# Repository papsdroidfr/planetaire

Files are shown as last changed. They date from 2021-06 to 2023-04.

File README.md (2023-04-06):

# planétaire

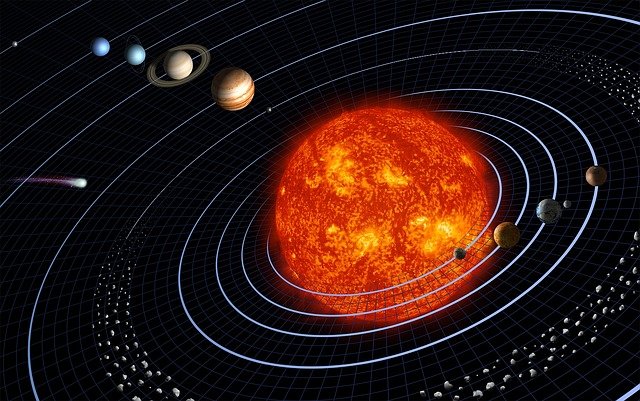
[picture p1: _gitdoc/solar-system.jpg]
système solaire


Ce projet consiste à réaliser un planétaire mécanique à l'échelle d'un bureau, à base d'impression 3D et d'électronique (Raspberry pico)

## cadrage du projet 

Quelques bases concernant [les dimensions](https://papsdroidfr.github.io/tutoriels/planetaire/) du système solaire

Notre planétaire mécanique à l'échelle d'un bureau va:
* représenter les orbites sous forme de cercles
* tricher sur les proportions des orbites et taille de Jupiter et Saturne (et du soleil)
* intégrer les 6 planètes visibles à l’œil nu: Mercure, Vénus, la Terre (et son satellite la lune), Mars, Jupiter et Saturne.

Un peu de théorie avec [les engrenages](https://papsdroidfr.github.io/tutoriels/engrenages/)
* les roues dentées utlisées doivent être limitées en nombre de dents (de 13 à 100)
* les engrenages simples (2 roues dentées) ne permettent pas d'obtenir de gros rapport de réduction R = -d1/d2 (avec 2 roues) ou R = +d1/d3 (avec 3 roues: le nombre de dents de la roue intermédiaire ne compte pas dans le rapport de réduction)
* les engrenages à étage permettent d'aller chercher les gros rapports de réduction selon l'équation:

```python
R = (-1)^y * (Z1 * Z2 *..* Zn) / (D1 * D2 * ... * Dm)
```

* y est le nombre de contacts entre les dents.
* Zi, Dj le nombre de dents d'une roue.
* n le nombre de roue menantes.
* m le nombre de roue menées.

## calcul des réduction d'engrenages 

le programme **engrenage_reduction.py** (dossier /python) calcule la meilleure solution d'engenages sur 2, 3 ou 4 étages pour obtenir un rapport de réduction R donné. Plus de détail dans [cet article](https://papsdroidfr.github.io/dev/CalculEngrenages/).

## Conception des étages d'engrenages par planète

### Mercure
La conception du prototype en 3D est expliquée [ici](https://papsdroidfr.github.io/tutoriels/Planetaire-Mercure/)

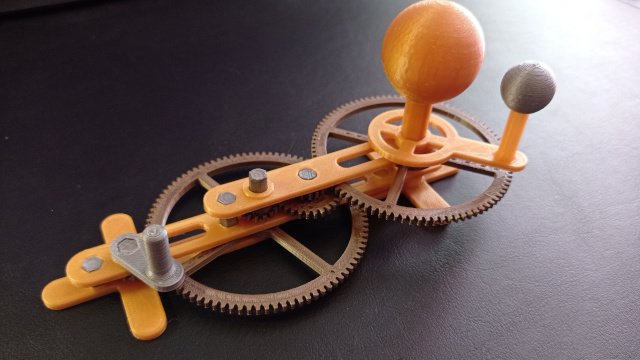
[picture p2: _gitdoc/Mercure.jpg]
Mercure


Ce premier prototype utilise un mécanismue de réduction 1/7 avec une roue de 13 dents contre une roue de 13*7=91 dents afin d'avoir un premier axe qui représente une jounée (celui où l'on retrouve la manivelle) et un second qui représente une semaine. Tous les mécanismes vont partir de l'axe des semaines, les rapports sont donc tous réduits par 7 dès le départ.

Mercure tourne autour du soleil en 87,969 jours ( =12,567 semaines). En utilisant des roues menantes de 14  et 15 dents contre des roues menées de 29 et 91 dents j'obtiens un rapport de réduction de 87,967.

### Vénus
conception du modèle 3D: [ici](https://papsdroidfr.github.io/tutoriels/Planetaire-Venus/)

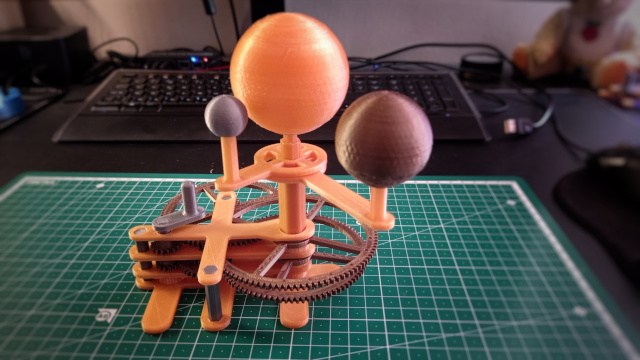
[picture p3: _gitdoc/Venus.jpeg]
Venus


Tous les mécanismes partent désormais de l'axe des semaines avec une réduction de 1/7 dès le départ.
On retrouve donc sur le premier plateau les roues de 14,15, 29 et 91 dents pour obtenir le rapport de réduction 87,967 propre à Mercure 
Le second plateau est quand à lui composé de 2 roues menantes de 16 dents contre des roues menées de 83 et 99 dents afin d'obtenir un rapport de réduction de 224.684 pour Vénus (Vénus tourne autour du soleil en 224,700 jours). On pourrait obtenir une meilleure précision en ajoutant un 2ème étage mais ce gain de précision n'en vaut pas la peine pour cette maquette qui n'a pas vocation à faire des prédictions.
Toutes les planètes sont positionnées sur des plateaux centrés sur des axes creux qui s'emboitent les uns dans les autres.

### Terre
conception du modèle 3D: [ici](https://papsdroidfr.github.io/tutoriels/planetaire-terre/)

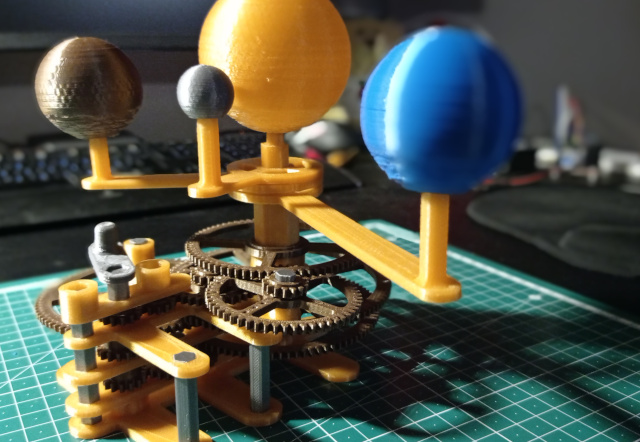
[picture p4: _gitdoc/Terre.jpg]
Terre


Pour rappel, j'utilise un axe commun pour toutes les planètes qui représente 1 semaine (7 jours) par tour complet. Tous les mécanismes héritent de fait de ce premier rapport de réduction de 1/7. Il faut donc viser 7/365,256 comme rapport de réduction. J'utilise mon programme développé en python pour simuler plusieurs solutions de manière à retenir le meilleur compromis entre précision et complexité (nombre d'étages d'engrenages). On arrive à une belle solution avec 2 étages de 3 peties roues menantes de 13, 15 et 15 dents, contre 3 grandes roues menées de 37, 55 et 75 dents. Si vous faites le calcul 7 * ( 37*55*75) / ( 13*15*15) vous verrez que la précision est diaboliquement proche de 365,256. Puisqu'il y a un étage de plus que pour Mercure et Vénus, il faut ajouter une roue inverseuse afin que la Terre tourne dans le même sens que les autres planètes.

### Mars
conception du modèle 3D: [ici](https://papsdroidfr.github.io/tutoriels/planetaire-mars/)

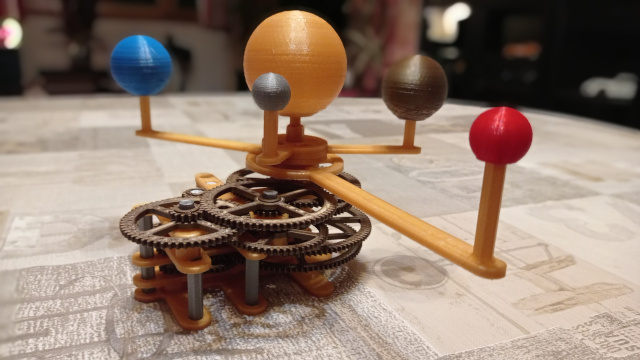
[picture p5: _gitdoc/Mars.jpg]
Mars


Je trouve un très bon compromis avec seulement 2 étages de 3 roues menantes de 14, 15 et 16 dents contre 3 roues menées de 59, 69 et 81 dents. Je rappelle que la première roue menante (celle de 14 dents en l’occurrence) est positionnée sur l'axe de rotation des semaines: il faut donc multiplier le tout par 7 pour avoir le rapport de réduction final: 7*(59*69*81)/(14*15*16) = 686,98125 : pas la peine de se compliquer la vie en rajoutant un 3me étage pour gagner en précision: c'est déjà très précis comme ça quand on vise à obtenir 686.980 ! Enfin une dernière petite astuce pour que Mars tourne dans le même sens que les autres planètes: je pars de l'axe de rotation hebdomadaire déjà inversé du mécanisme de la Terre. L'axe central qui soutient le bras sur lequel Mars est positionnée est quand à lui centré sur l'axe du soleil, et enveloppe les axes respectifs de Mercure, Vénus et celui de la Terre: ils sont tous à l'intérieur.

### Notice de montage 
La notice de montage complète, avec motirisation optionnelle, est décrite [dans cet article](https://papsdroidfr.github.io/tutoriels/planetaire-maquette/)

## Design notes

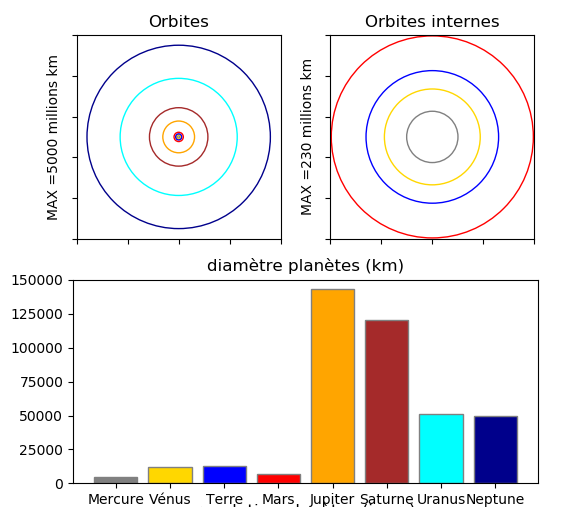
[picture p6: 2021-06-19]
_gitdoc/orbites.png

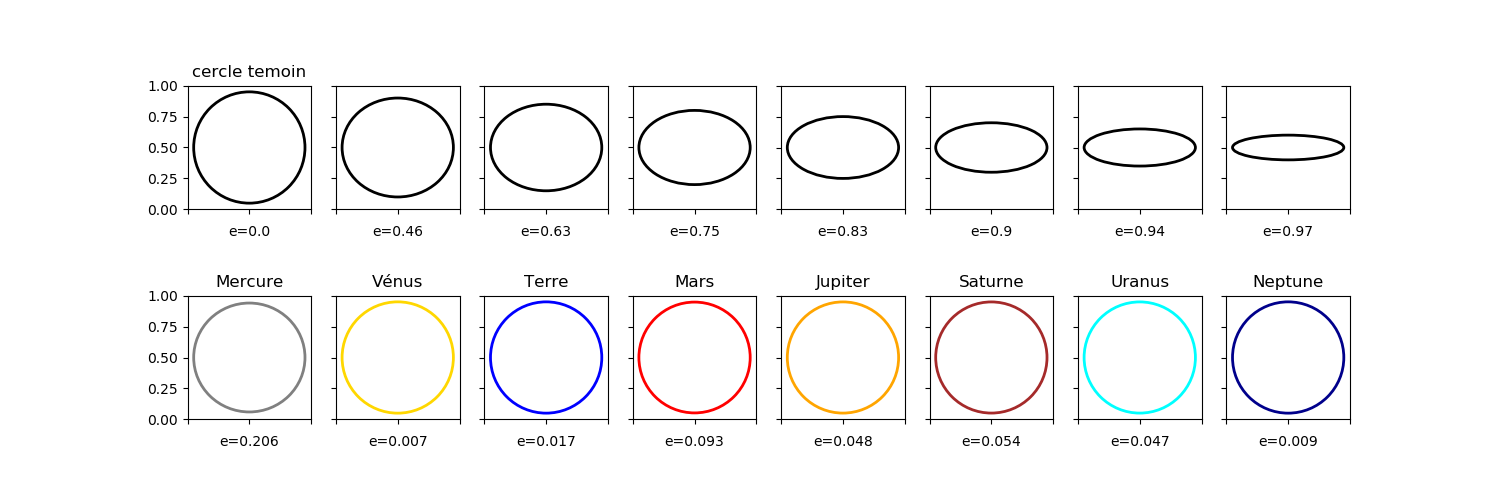
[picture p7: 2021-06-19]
_gitdoc/ellipses.png

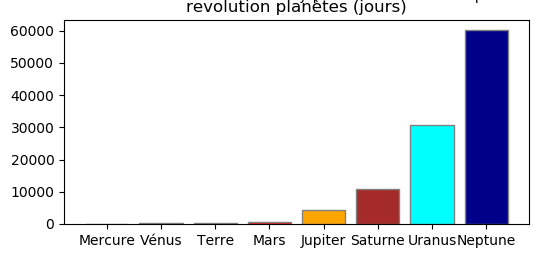
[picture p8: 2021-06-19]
_gitdoc/revolutions.png

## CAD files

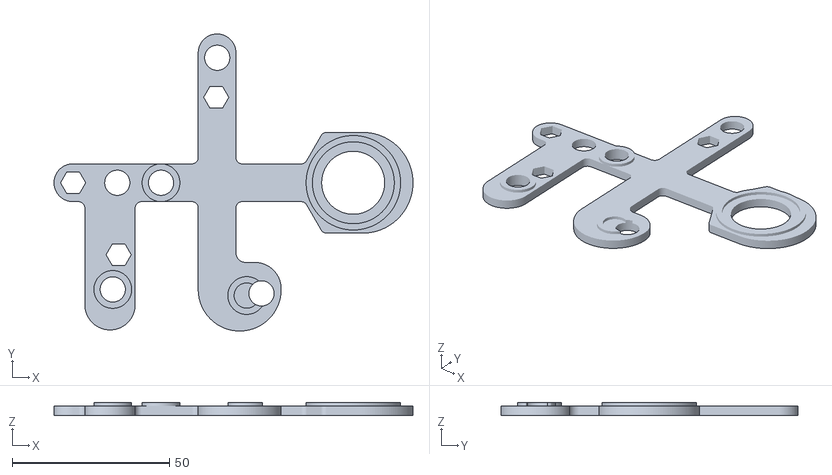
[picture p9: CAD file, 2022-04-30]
STLPlanetaire/Mars/Mars_Support_Bas.stl
114.0 x 94.3 x 4.00

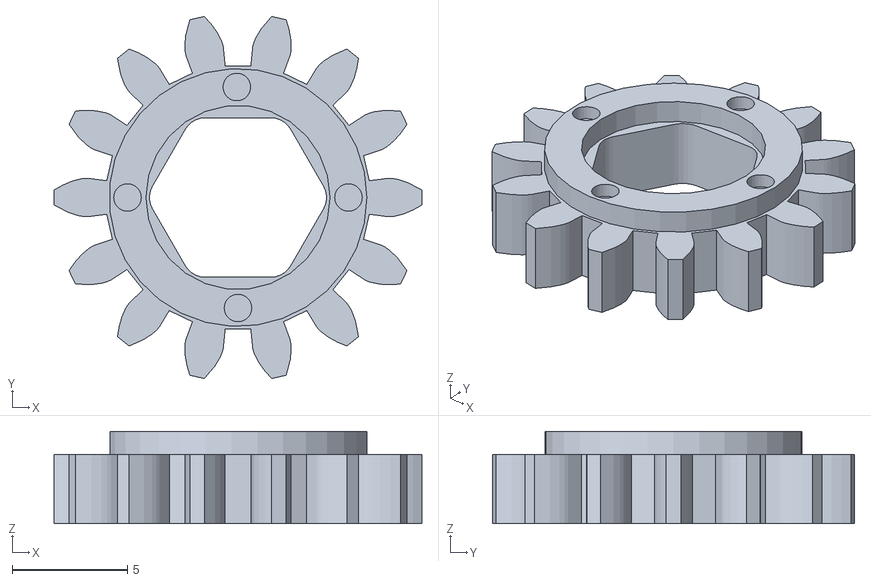
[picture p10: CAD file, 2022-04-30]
STLPlanetaire/Mercure/mercure_gear14.stl
16.0 x 15.7 x 4.00

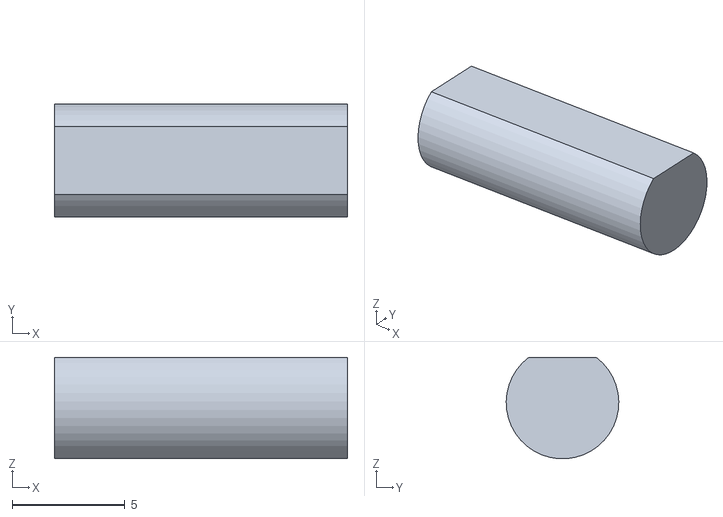
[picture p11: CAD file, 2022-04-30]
STLPlanetaire/MOTOR/moteurSupportAxe.stl
13.0 x 5.00 x 4.49

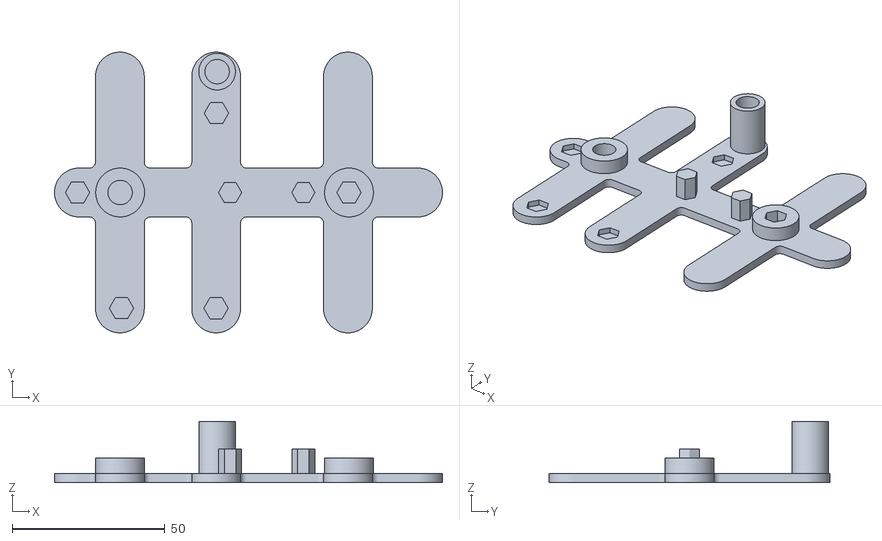
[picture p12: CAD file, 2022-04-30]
STLPlanetaire/Pied/pied_support_bas.stl
127.1 x 92.0 x 20.0

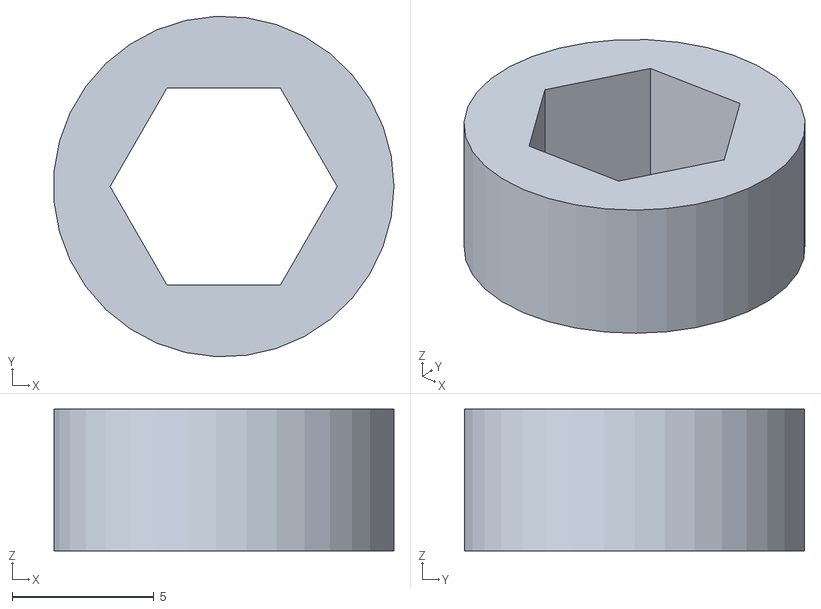
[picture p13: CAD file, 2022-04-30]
STLPlanetaire/Soleil/soleilColeretteAxe.stl
12.0 x 12.0 x 5.00

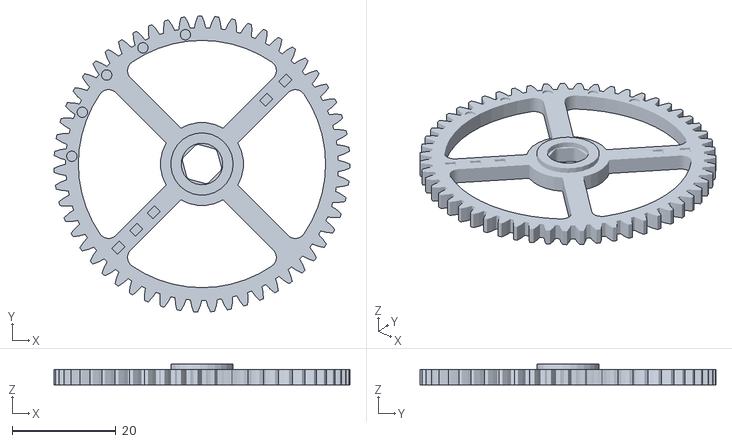
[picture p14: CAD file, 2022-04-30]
STLPlanetaire/Terre/TerreGear55.stl
57.0 x 57.0 x 4.00

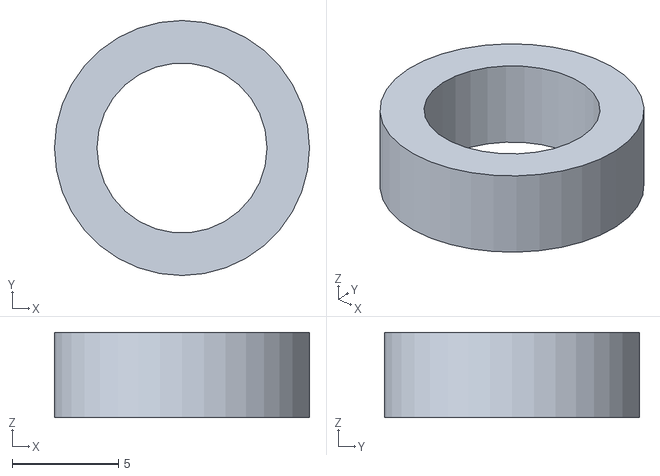
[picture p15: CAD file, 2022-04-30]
STLPlanetaire/Vénus/venus_colerette.stl
12.0 x 12.0 x 4.00

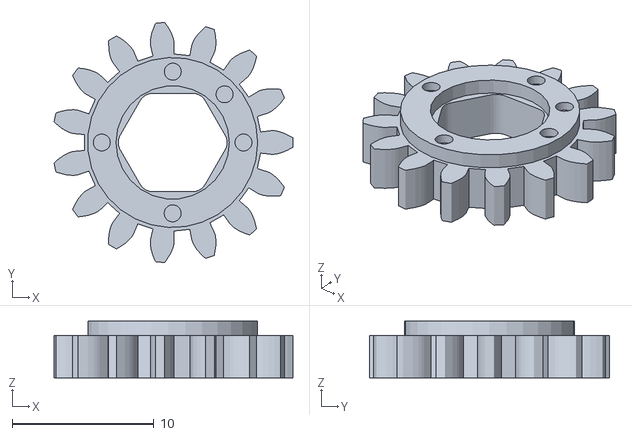
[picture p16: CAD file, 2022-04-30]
STLPlanetaire/Mars/Mars_Gear15.stl
16.9 x 17.0 x 4.00

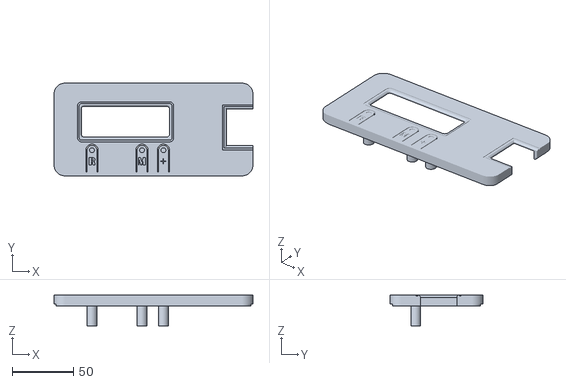
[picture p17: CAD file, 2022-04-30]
STLPlanetaire/MOTOR/BoitierHaut.stl
162.9 x 75.9 x 25.0

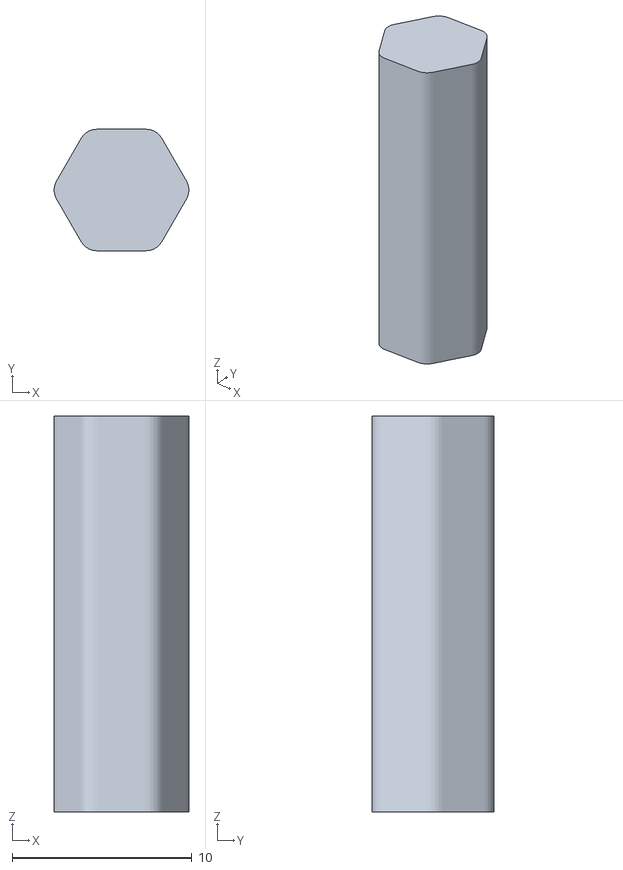
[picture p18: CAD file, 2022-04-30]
STLPlanetaire/Pied/pied_fix3.stl
7.48 x 6.75 x 22.0

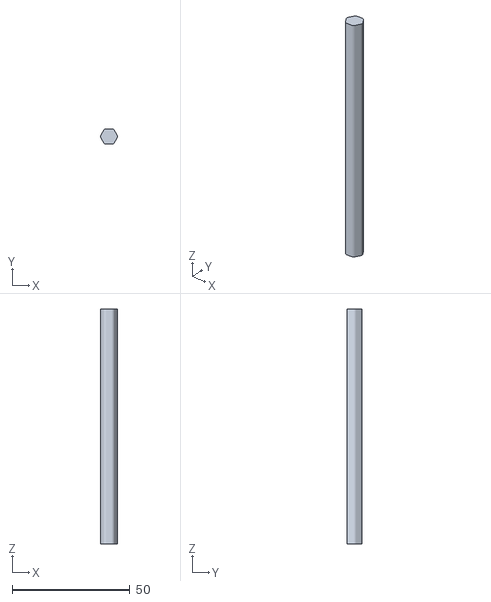
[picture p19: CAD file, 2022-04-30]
STLPlanetaire/Soleil/axeSoleil.stl
7.17 x 6.58 x 100.0

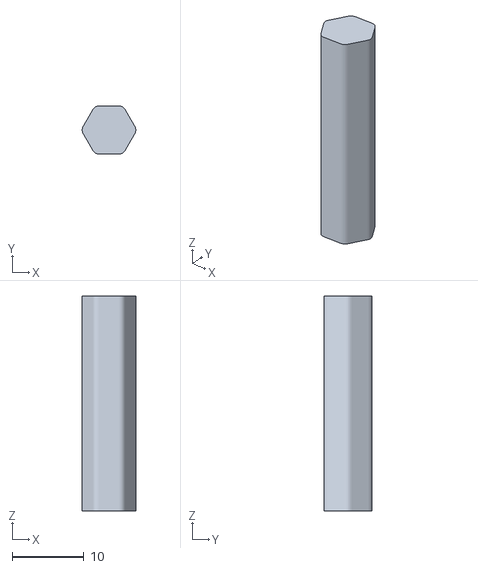
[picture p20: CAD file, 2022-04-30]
STLPlanetaire/Terre/Terre_AxeFix.stl
7.48 x 6.75 x 30.0

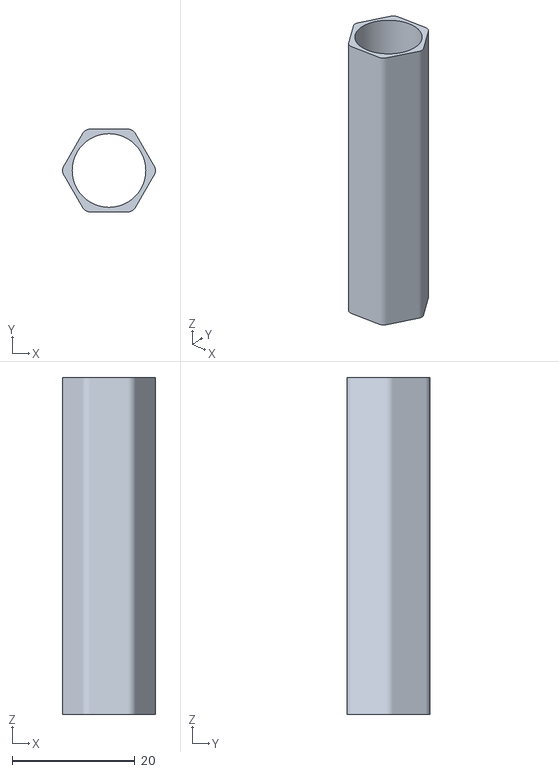
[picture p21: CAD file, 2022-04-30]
STLPlanetaire/Vénus/venus_axe.stl
15.2 x 13.5 x 55.0

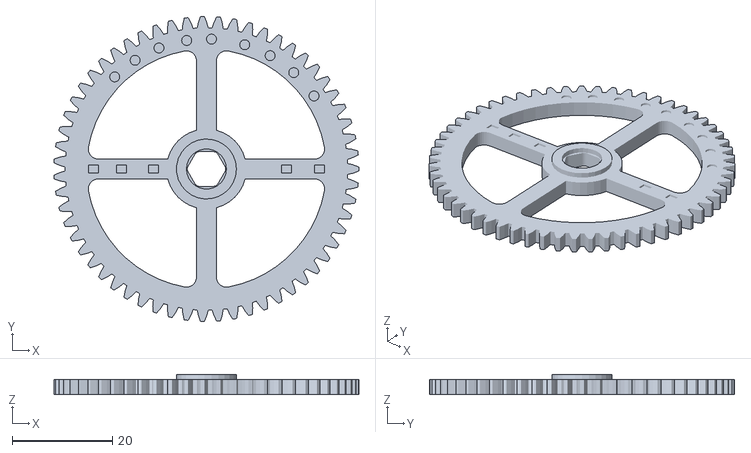
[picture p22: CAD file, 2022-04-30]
STLPlanetaire/Mars/Mars_Gear59.stl
61.0 x 61.0 x 4.00

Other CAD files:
STLPlanetaire/Mercure/mercure_colerette.stl
STLPlanetaire/Mercure/mercureColeretteAxe.stl
STLPlanetaire/MOTOR/moteurGear14.stl
STLPlanetaire/Pied/pied_fix1.stl
STLPlanetaire/MOTOR/BoitierBas.stl
STLPlanetaire/MOTOR/moteurGear16.stl
STLPlanetaire/MOTOR/moteurSupportBas.stl
STLPlanetaire/Mars/MarsColerette4mm.stl
STLPlanetaire/Mars/Mars_Axe_Central.stl
STLPlanetaire/Mars/Mars_Axe_Gear59.stl
STLPlanetaire/Mars/Mars_Axe_Gear69.stl
STLPlanetaire/Mars/Mars_Axe_fix(x2).stl
STLPlanetaire/Mars/Mars_Gear14.stl
STLPlanetaire/Mars/Mars_Gear16.stl
STLPlanetaire/Mars/Mars_Gear69.stl
STLPlanetaire/Mars/Mars_Gear81.stl
STLPlanetaire/Mars/Mars_Panète.stl
STLPlanetaire/Mars/Mars_Plateau.stl
STLPlanetaire/Mars/Mars_Support_Haut.stl
STLPlanetaire/Mercure/Mercure_support_bas.stl
STLPlanetaire/Mercure/mercure.stl
STLPlanetaire/Mercure/mercure_axe_central.stl
STLPlanetaire/Mercure/mercure_axe_gear.stl
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

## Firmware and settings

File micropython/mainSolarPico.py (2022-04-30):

#RUNS ON PICO
from bipolarStepper import BipolarStepper
from machine import Pin, I2C, Timer
from machine_i2c_lcd import I2cLcd
import sys, time, _thread


class MyLCD:
    ''' LCD1602 screen '''
    def __init__(self):
        
        #i2c detection
        i2c = I2C(0, sda=Pin(0), scl=Pin(1), freq=400000)
        l=i2c.scan() #liste les adresses I2C trouvées
        try:   
            i2c_adr = hex(l[0])
            print('Init LCD, adresse I2C: ', i2c_adr)
        except:
            print('aucun LCD I2C trouvé, vérifiez vos branchements...')
            sys.exit()
        
        self.lcd = I2cLcd(i2c, int(i2c_adr), 2, 16)
        
        # generator custom character: http://omerk.github.io/lcdchargen/
        charmap = [
            #chr(0): logo papsdroid
            [0b01110,0b11111,0b10101,0b11111,0b11111,0b10001,0b11111,0b01110],
            #chr(1): fusée
            [0b00100,0b01110,0b01010,0b11111,0b11111,0b11111,0b10101,0b10001],
            #chr(2): pi
            [0b00000,0b00000,0b11111,0b01010,0b01010,0b01010,0b10011,0b00000],
            #chr(3): batterie full
            [0b01110,0b11011,0b10001,0b10101,0b10101,0b10101,0b10001,0b11111],
        ]
        for i in range(len(charmap)):
            self.lcd.custom_char(i,charmap[i])
        
        self.id_day=0    # updated with motor rotation
        self.id_mode=0   # updated with mode change
        self.mode=''     # updated with mode change
    
        self.msg_init()
    
    def msg_init(self):
        '''displsay init message'''
        self.lcd.clear()
        self.lcd.move_to(0,0)
        self.lcd.putchar(chr(0)) #logo paspdroid
        self.lcd.putstr(' PapsDroid.fr ')
        self.lcd.putchar(chr(0))
        self.lcd.putchar(chr(2))
        self.lcd.putstr('\n'+' PICOPLANETES ')
        self.lcd.putchar(chr(2))
        time.sleep(1)
       
    def displ_mode(self):
        ''' display mode'''
        self.lcd.move_to(0,0)
        self.lcd.putstr('Mode: ')
        for _i in range(self.id_mode+1):
            self.lcd.putchar(chr(3))
        for _i in range(4-self.id_mode):
            self.lcd.putchar(' ')
        self.lcd.move_to(12,0)
        self.lcd.putstr(self.mode)
        
        
    def displ_jour(self, _tm):
        '''display day number, called in Timer every 200ms'''
        str_day = str(self.id_day)
        self.lcd.move_to(0,1)
        self.lcd.putstr('Jour: ' + str_day)
    
class Application:
    
    def __init__(self):
        ''' initialize lcd, push Button and stepper motor'''
        self.mylcd = MyLCD();
        self.ledStatus = Pin(25, Pin.OUT)     # led témoin du pico
        self.buttonMode = Pin(18, Pin.IN, Pin.PULL_DOWN) #bouton poussoir avec resistance de rappel activée
        self.buttonNext = Pin(19, Pin.IN, Pin.PULL_DOWN) #bouton poussoir avec resistance de rappel activée
        self.id_mode=0
        self.l_modes = ['+01J', '+07J', '+30J', '+inf']
        self.bouncetime = 0.05 #stabilization period with push buttons
        #callback function called with push buttons
        self.buttonMode.irq(self.callbackMode, Pin.IRQ_FALLING)
        self.buttonNext.irq(self.callbackNext, Pin.IRQ_FALLING)
        self.buttonModePressed = False #button not pressed
        self.buttonNextPressed = False #button not pressed
        self.bp = BipolarStepper()     #stepper motor
        self.l_step_day = self.bp.split_steps(7) # split steps into 7 phases
        self.id_day = 0
        self.motorON = False       # False: motor is Off, True: motor is On
        self.ledStatus.value(0)    # led pico off
        #init motor
        self.bp.set_speed('low')
        self.bp.next_steps(nsteps=100)
        self.bp.set_speed('high')
        self.mylcd.lcd.clear()
        self.mylcd.mode = self.l_modes[self.id_mode]
        self.mylcd.id_day = self.id_day
        self.mylcd.displ_mode()
        #self.mylcd.displ_jour()
        self.timLCD = Timer(period=200, callback=self.mylcd.displ_jour) #timer update LCD toutes les 200 ms
        self.loop()  #inifinite loop of events     
    
    def callbackMode(self, pin):
        ''' callback function called when buttonMode is pushed '''
        time.sleep(self.bouncetime)      # wait stabilization to avoid rebounds.
        if not(self.buttonMode.value()): # push button still pressed after the stabilization period ?
            if (self.buttonModePressed == False) : # run only 1 time the callbac
                self.buttonModePressed = True
                self.id_mode = (self.id_mode + 1) % len(self.l_modes) # next mode
                #print('mode: ', self.l_modes[self.id_mode])
                self.mylcd.id_mode = self.id_mode
                self.mylcd.mode = self.l_modes[self.id_mode]
                self.mylcd.displ_mode()
 
    def callbackNext(self, pin):
        ''' callback function called when buttonNext is pushed '''
        time.sleep(self.bouncetime)      # wait stabilization to avoid rebounds.
        if not(self.buttonNext.value()): # push button still pressed after the stabilization period ?
            if (self.buttonNextPressed == False) : # run only 1 time the callback
                self.buttonNextPressed = True
       
    def move_1_day(self):
        ''' rotate stepper motor for 1 day '''
        self.id_day += 1
        #print('day: ', self.id_day)
        self.mylcd.id_day = self.id_day
        self.bp.next_steps(nsteps=self.l_step_day[self.id_day % 7]) #move motor: next day

    def move_1_week(self):
        ''' rotate stepper motor for 1 week '''
        for _i in range(7):
            self.move_1_day()

    def move_4_weeks(self):
        ''' rotate stepper motor for 4 weeks '''
        for _i in range(30):
            self.move_1_day()

    def loop(self):
        ''' infinite loop of events '''
        while(True):

            self.buttonModePressed = False           
 
            #gestion du moteur, bouton 'next' pressé
            if self.buttonNextPressed :
                if self.id_mode <3 :
                    self.motorON = True
                    self.ledStatus.value(1)   #led pico on
                    if (self.id_mode == 0):
                        self.move_1_day()
                    elif (self.id_mode == 1):
                        self.move_1_week()
                    else:
                        self.move_4_weeks()
                    self.ledStatus.value(0)   #led pico off
                    self.motorON = False
            
                #mode infini 
                else:
                    self.motorON = not(self.motorON)
                    #gestion alumage pico led
                    self.ledStatus.value(self.motorON) 

                self.buttonNextPressed = False
            
            #mode infini et motor ON
            if (self.id_mode==3 and self.motorON):
                self.move_1_day()           
            else:
                time.sleep(0.2)

appl=Application()

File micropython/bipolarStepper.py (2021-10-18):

# bipolar stepper motor controled by L298N & Raspberry PICO
# https://www.papsdroid.fr
# October 2021

from machine import Pin
import utime

class BipolarStepper():
    ''' bipolar stepper motor controled by L298N & Raspberry PICO
            In1 - pin14 - A
            In2 - pin15 - A/
            In3 - pin16 - B
            In4 - pin17 - B/
        init parameters
            speed: 'high' (default), 'medium', 'low', or 'test'
            direction: 'forward' (default) , 'backward'
        methods:
            set_direction(direction) # set direction either 'forward' or 'backward'
            set_speed(speed)         # set motor speed (delay between 2 steps)
            next_step(nbsteps)       # move motor *nsteps
        
        example:
            bp = BipolarStepper(speed='medium')
            bp.next_step(100) # move 100 steps forward speed medium
            bp.set_direction('backward')
            bp.set_speed('high')
            bp.next_step(50) # move 50 steps backward highest speed
        
    '''
    # constructor
    def __init__(self, speed='high', direction='forward', steps360=200):
        ''' constructor
            speed = 'high' (default), 'medium', 'low', 'test'
            direction = 'forward' (default), 'backward'
            steps360 (200 default): nb of steps to rotate 360°
        '''
        #speed motor: delays between 2 steps
        self.speed = {'high': 0.005,   # 5ms delay between 2 steps
                      'medium': 0.008, # 8ms delay between 2 steps
                      'low': 0.016,    # 20ms delay between 2 steps
                      'test':0.5,      # 0.5s delay between 2 steps for testing activity
                      }
        self.set_speed(speed)
        #direction forward or backward
        self.dic_direction = { 'forward':1, 'backward':-1 }
        self.set_direction(direction)
        self.steps360 = steps360
        #Raspberry PICO pins output
        self.pins = [
            Pin(14, Pin.OUT), #IN1 - A  - BLACK
            Pin(15, Pin.OUT), #IN2 - A\ - GREEN
            Pin(16, Pin.OUT), #IN3 - B  - RED
            Pin(17, Pin.OUT)] #IN4 - B\ - BLUE
        # sequences to run in circle
        self.full_step_seq = [ 
            [1,0,1,0], # AB 
            [0,1,1,0], # A/B 
            [0,1,0,1], # A/B/
            [1,0,0,1]] # AB/
        self.seq = 0   # current sequence: 0,1,2,3
        #init motor with first position seq 0
        print('init motor')
        self.move_motor()
        utime.sleep(0.5)

    # Private methods
    # -------------------------------------------------
    
    def move_motor(self):
        ''' move motor to curent step and wait
        '''
        #run current sequence
        for i in range(4):
            self.pins[i].value(self.full_step_seq[self.seq][i])
        utime.sleep(self.delay)


    # Public methods
    # ---------------------------------------------------------------
    
    def set_speed(self, speed):
        ''' motor speed: 'high' (default), 'medium', 'low' or 'test'
        '''
        try:
            self.delay = self.speed[speed]
        except:
            self.delay = self.speed['high']
    
    def set_direction(self, direction):
        ''' set direction either forward (default) or backward
        '''
        try:
            self.direction = self.dic_direction[direction]
        except:
            self.direction = self.dic_direction['forward']          
    
    def next_steps(self, nsteps=1):
        ''' move motor to the next sequence * nsteps
        '''
        for i in range(nsteps):
            self.seq = (self.seq + self.direction)%4
            self.move_motor()          

    def next_angle(self, angle=90):
        ''' move motor nsteps = steps360*angle//360 '''
        self.next_steps(self.steps360*angle//360)
    
    def split_steps(self, nsplits=1):
        ''' split steps360 into a list of nsplits equivalent steps
        '''
        l = nsplits*[self.steps360//nsplits] # list of nsplits equal steps
        r = self.steps360%nsplits   # add this value, so that sum of steps = steps360
        for i in range(r):
            l[-1-i]+= 1 #r value added from the end of the list
        return l
        

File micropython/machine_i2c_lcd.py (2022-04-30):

"""Implements a HD44780 character LCD connected via PCF8574 on I2C.
   This was tested with: https://www.wemos.cc/product/d1-mini.html"""

from lcd_api import LcdApi
from machine import I2C
from time import sleep_ms

# The PCF8574 has a jumper selectable address: 0x20 - 0x27
DEFAULT_I2C_ADDR = 0x27

# Defines shifts or masks for the various LCD line attached to the PCF8574

MASK_RS = 0x01
MASK_RW = 0x02
MASK_E = 0x04
SHIFT_BACKLIGHT = 3
SHIFT_DATA = 4


class I2cLcd(LcdApi):
    """Implements a HD44780 character LCD connected via PCF8574 on I2C."""

    def __init__(self, i2c, i2c_addr, num_lines, num_columns):
        self.i2c = i2c
        self.i2c_addr = i2c_addr
        self.i2c.writeto(self.i2c_addr, bytearray([0]))
        sleep_ms(20)   # Allow LCD time to powerup
        # Send reset 3 times
        self.hal_write_init_nibble(self.LCD_FUNCTION_RESET)
        sleep_ms(5)    # need to delay at least 4.1 msec
        self.hal_write_init_nibble(self.LCD_FUNCTION_RESET)
        sleep_ms(1)
        self.hal_write_init_nibble(self.LCD_FUNCTION_RESET)
        sleep_ms(1)
        # Put LCD into 4 bit mode
        self.hal_write_init_nibble(self.LCD_FUNCTION)
        sleep_ms(1)
        LcdApi.__init__(self, num_lines, num_columns)
        cmd = self.LCD_FUNCTION
        if num_lines > 1:
            cmd |= self.LCD_FUNCTION_2LINES
        self.hal_write_command(cmd)

    def hal_write_init_nibble(self, nibble):
        """Writes an initialization nibble to the LCD.
        This particular function is only used during initialization.
        """
        byte = ((nibble >> 4) & 0x0f) << SHIFT_DATA
        self.i2c.writeto(self.i2c_addr, bytearray([byte | MASK_E]))
        self.i2c.writeto(self.i2c_addr, bytearray([byte]))

    def hal_backlight_on(self):
        """Allows the hal layer to turn the backlight on."""
        self.i2c.writeto(self.i2c_addr, bytearray([1 << SHIFT_BACKLIGHT]))

    def hal_backlight_off(self):
        """Allows the hal layer to turn the backlight off."""
        self.i2c.writeto(self.i2c_addr, bytearray([0]))

    def hal_write_command(self, cmd):
        """Writes a command to the LCD.
        Data is latched on the falling edge of E.
        """
        byte = ((self.backlight << SHIFT_BACKLIGHT) | (((cmd >> 4) & 0x0f) << SHIFT_DATA))
        self.i2c.writeto(self.i2c_addr, bytearray([byte | MASK_E]))
        self.i2c.writeto(self.i2c_addr, bytearray([byte]))
        byte = ((self.backlight << SHIFT_BACKLIGHT) | ((cmd & 0x0f) << SHIFT_DATA))
        self.i2c.writeto(self.i2c_addr, bytearray([byte | MASK_E]))
        self.i2c.writeto(self.i2c_addr, bytearray([byte]))
        if cmd <= 3:
            # The home and clear commands require a worst case delay of 4.1 msec
            sleep_ms(5)

    def hal_write_data(self, data):
        """Write data to the LCD."""
        byte = (MASK_RS | (self.backlight << SHIFT_BACKLIGHT) | (((data >> 4) & 0x0f) << SHIFT_DATA))
        self.i2c.writeto(self.i2c_addr, bytearray([byte | MASK_E]))
        self.i2c.writeto(self.i2c_addr, bytearray([byte]))
        byte = (MASK_RS | (self.backlight << SHIFT_BACKLIGHT) | ((data & 0x0f) << SHIFT_DATA))
        self.i2c.writeto(self.i2c_addr, bytearray([byte | MASK_E]))
        self.i2c.writeto(self.i2c_addr, bytearray([byte]))
